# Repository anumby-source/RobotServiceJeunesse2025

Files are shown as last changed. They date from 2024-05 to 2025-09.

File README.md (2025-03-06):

# RobotServiceJeunesse2025
Développements pour la séance Service Jeunesse au printemps 2025

# Structure pour le R&D
* Chaque développeur se voit attribué un espace à son nom pour ses propres développements de R&D
* Données pour le véhicule du service jeunesse 2025

Ultérieurement, lorsque l'on aura sélectionné les choix de design et de technologie, on assemblera les développements communs

# Utilisation de Fusion 360 pour l'impression 3D

On peut démarrer cette série de tuto Youtube en mode "très débutant". Un peu lent mais clair. 1, 2, 3, 4, ...

* [Fusion 360 Complet Débutant](https://www.youtube.com/watch?v=3kL6a9yyus8&list=PL0qHSH9_1qY5kvUzO7SlggBShYAllfP7j&index=4)
* [Modélisation une Loupe en français](https://www.youtube.com/watch?v=21fNvLuIeyk&list=PL0qHSH9_1qY5kvUzO7SlggBShYAllfP7j&index=1)
* [Modélisation d'une attache type GoPro](https://www.youtube.com/watch?v=NfXD1W5tZaM&list=PL0qHSH9_1qY5kvUzO7SlggBShYAllfP7j&index=2)
* [Croquis, Contraintes, Dimensions](https://www.youtube.com/watch?v=1mFSI_tEmsY&list=PL0qHSH9_1qY5kvUzO7SlggBShYAllfP7j&index=3)
* [Tournevis à Embout - Régle d'Or, Volumes et Composants](https://www.youtube.com/watch?v=3kL6a9yyus8&list=PL0qHSH9_1qY5kvUzO7SlggBShYAllfP7j&index=4)
* [Bielle et Piston: Jointure, Articulations, Mouvements.](https://www.youtube.com/watch?v=oicK9lwJ6bA&list=PL0qHSH9_1qY5kvUzO7SlggBShYAllfP7j&index=5)
* [Organisation d'un projet et Régle d'Or](https://www.youtube.com/watch?v=NAn41hFw8Yg&list=PL0qHSH9_1qY5kvUzO7SlggBShYAllfP7j&index=6)
* [Tolérances, Historique, Colorisation](https://www.youtube.com/watch?v=N-1HDvVJG_U&list=PL0qHSH9_1qY5kvUzO7SlggBShYAllfP7j&index=7)
* [Survol des "Ateliers"](https://www.youtube.com/watch?v=0DFtvFfrYvw&list=PL0qHSH9_1qY5kvUzO7SlggBShYAllfP7j&index=8)
* [Loft et Sweep](https://www.youtube.com/watch?v=eku9RZ19Kuo&list=PL0qHSH9_1qY5kvUzO7SlggBShYAllfP7j&index=9)
* [Construction Coque de Bateau - Etape 1](https://www.youtube.com/watch?v=NDEB2YS3qxY&list=PL0qHSH9_1qY5kvUzO7SlggBShYAllfP7j&index=10)
* [Construction Coque de Bateau Etape 2](https://www.youtube.com/watch?v=uyDRabeoyRY&list=PL0qHSH9_1qY5kvUzO7SlggBShYAllfP7j&index=11)
* [Extensions (add-ins) et Scripts](https://www.youtube.com/watch?v=a0wj_iS4hvU&list=PL0qHSH9_1qY5kvUzO7SlggBShYAllfP7j&index=12)
* [Coque Minute avec Patch](https://www.youtube.com/watch?v=YINleWgpdjY&list=PL0qHSH9_1qY5kvUzO7SlggBShYAllfP7j&index=13)
* [Apprendre en faisant n'importe quoi!](https://www.youtube.com/watch?v=OFpFc8LrxU4&list=PL0qHSH9_1qY5kvUzO7SlggBShYAllfP7j&index=14)
* [Organisation, Composants, Bodies, Ensembles](https://www.youtube.com/watch?v=pDECKXFHmOQ&list=PL0qHSH9_1qY5kvUzO7SlggBShYAllfP7j&index=15)
* [Conception paramétrique sans paramètres (Où pas?)](https://www.youtube.com/watch?v=bImEM7l9Zes&list=PL0qHSH9_1qY5kvUzO7SlggBShYAllfP7j&index=16)
* [Nouvelle Interface? Pas de panique!](https://www.youtube.com/watch?v=ow5COcHA7XY&list=PL0qHSH9_1qY5kvUzO7SlggBShYAllfP7j&index=17)
* [Réconcilier (Enfin!) les Meshes avec Fusion 360](https://www.youtube.com/watch?v=rIGUrBB8rrw&list=PL0qHSH9_1qY5kvUzO7SlggBShYAllfP7j&index=18)
* [Vous allez aimer les contraintes (dans Fusion 360)](https://www.youtube.com/watch?v=fWU2rNBqDFI&list=PL0qHSH9_1qY5kvUzO7SlggBShYAllfP7j&index=19)
* [Super Mercis !!!!](https://www.youtube.com/watch?v=ioGxxQVQzVY&list=PL0qHSH9_1qY5kvUzO7SlggBShYAllfP7j&index=20)

Autre série pour Fusion 360 (2 séries: débutants, confirmés)

* [TUTORIELS FUSION 360](https://www.youtube.com/channel/UC1f3yfI3YFzhuoScarGSKwA)

TinkerCAD

* [TinkerCAD](https://www.youtube.com/watch?v=egNBQ0hXe2o)
* [TinkerCAD2](https://www.youtube.com/watch?v=DtlmVaoMNMc)

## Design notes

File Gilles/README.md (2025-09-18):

# Developpement pour le Robot Service Jeunesse 2025

<p align="center"> 
robot-2
robot-1
<p/>

<p align="center"> 
Telecommande
<p/>
  
<p align="center"> 
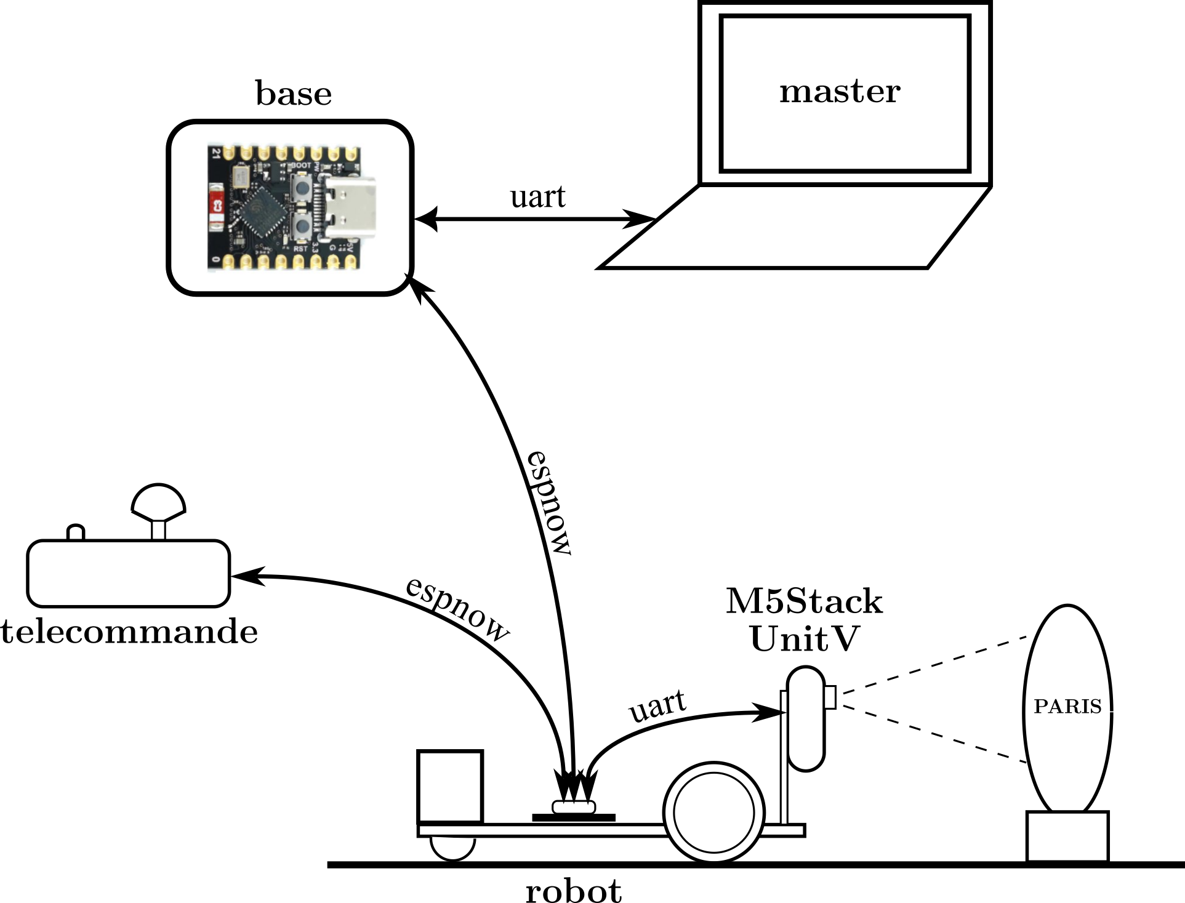
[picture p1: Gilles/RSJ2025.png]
   
<p/>

## Fonctionnement

- télécommande : elle lit la position du joystick, la transcrit en commande de vitesse des deux moteurs
  et envoie cette commande au robot à une fréquence de 10 Hz.

- M5Stack UnitV (K210) :

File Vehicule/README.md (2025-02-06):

# Dossiers pour les développements Electroniques pour le véhicule

* **Kicad** contient tous les développements électroniques
* plusieurs dossiers contiennent des documentations utilisées lors de la définition des éléments Kicad
  * **ESP32-C3**
  * **Joystick**
  * **Régulateur-DFR0569**

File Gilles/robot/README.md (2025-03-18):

## Développement robot

Les fichiers de pcb contenus dans ce répertoire sont ceux du prototype

Pour le pcb définitif, voir le répertoire **Kicad_9.0**

### Schéma électrique

<p align="center"> 
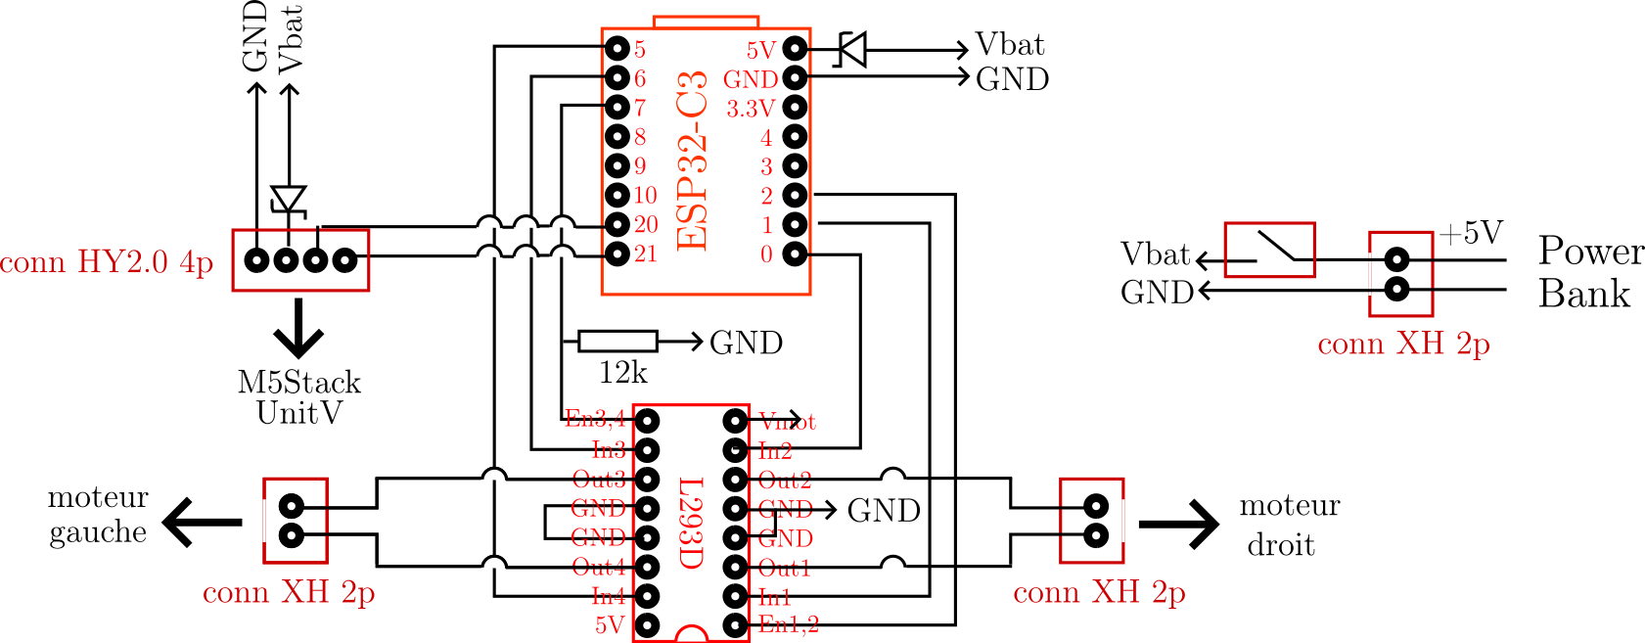
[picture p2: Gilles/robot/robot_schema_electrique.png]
   
<p/>

  ### PCB

<p align="center"> 
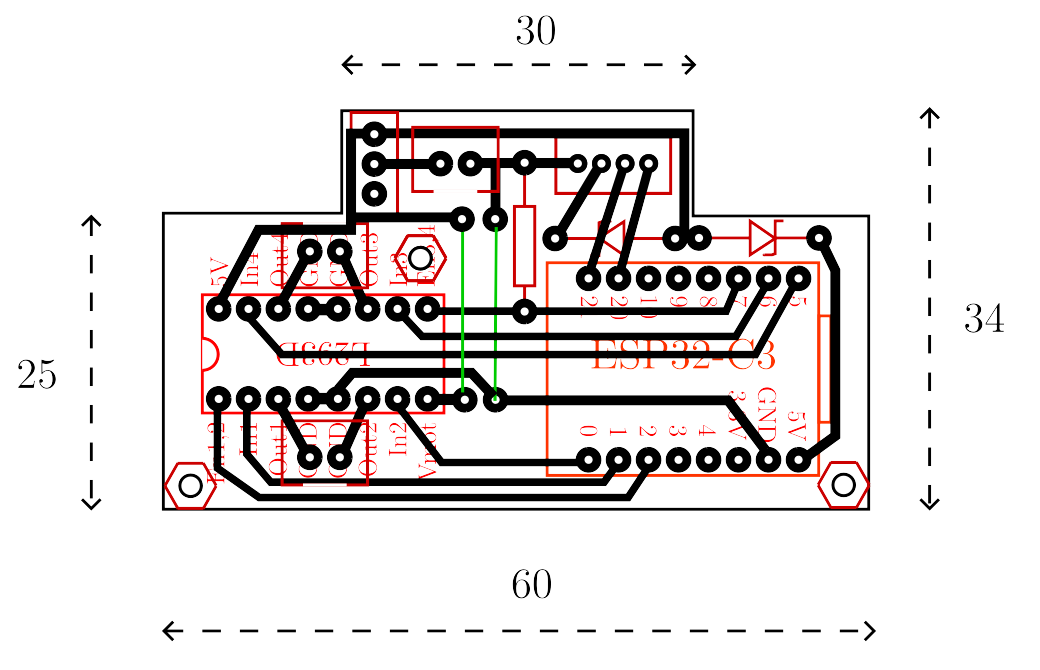
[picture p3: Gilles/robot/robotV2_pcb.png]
  
<p/>

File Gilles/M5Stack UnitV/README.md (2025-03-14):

## Reconnaissance de panneaux de signalisation avec la carte M5Stack UnitV

voir :     https://wiki.sipeed.com/soft/maixpy/en/course/ai/image/self_learn_classifier.html

### 1) Créer un compte sur MaixHub : 
    
    https://maixhub.com

### 2) Récupération du code machine du module M5Stack UnitV (nécessaire pour télécharger le modèle):
   
   voir https://maixhub.com/share/6
   - se logger sur le site MaixHub
   - télécharger key.gen.bin (https://dl.sipeed.com/shareURL/MaixHub_Tools) et le flasher avec 
     kflash_gui sur la carte UnitV à l'adresse 0X000000
   - lancer un terminal (screen, putty, …) et rebooter la carte. Le code apparait dans la fenêtre.

### 3) Installer le firmware : 

Flasher le firmrware (fichier _M5StickV_Firmware_v5.1.2.kfpkg_) avec kflash_gui

Flash firmware

### 4) Télécharger le modèle sur MaixHub (utiliser le code machine récupéré au 2) ) :
     
     https://maixhub.com/model/zoo/61
   
et le charger sur la carte avec kflash_gui à l'adresse 0X300000

Flash kmodel

### 5) Sur une carte micro-SD, charger _3_panneaux.classifier_ et _classify.py_
   
Inserer la carte micro-SD dans le M5Stack UnitV et lancer le script _classify.py_ 

Il est aussi possible de charger des fichiers (en particulier 3_panneaux.classifier) directement dans la mémoire flash de la M5Stack UnitV, sans utiliser la carte SD, dans MaixPy IDE : onglet "Tools > transfert file to board".

Pour chaque panneau reconnu, la led de la carte s'allume :
   - rouge -> stop
   - vert -> sens interdit
   - bleu -> dépassement interdit

## Connecteur Grove 

* 4 - GND noir
* 3 - VCC orange
* 2 - TX/SDA jaune
* 1 - RX/SCL blanc

* 
* 
*

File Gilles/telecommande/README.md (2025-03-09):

## Développements télécommande

Les fichiers de pcb contenus dans ce répertoire sont ceux du prototype

Pour le pcb définitif, voir le répertoire **Kicad_9.0**

### PCB - Implantation
<p align="center"> 
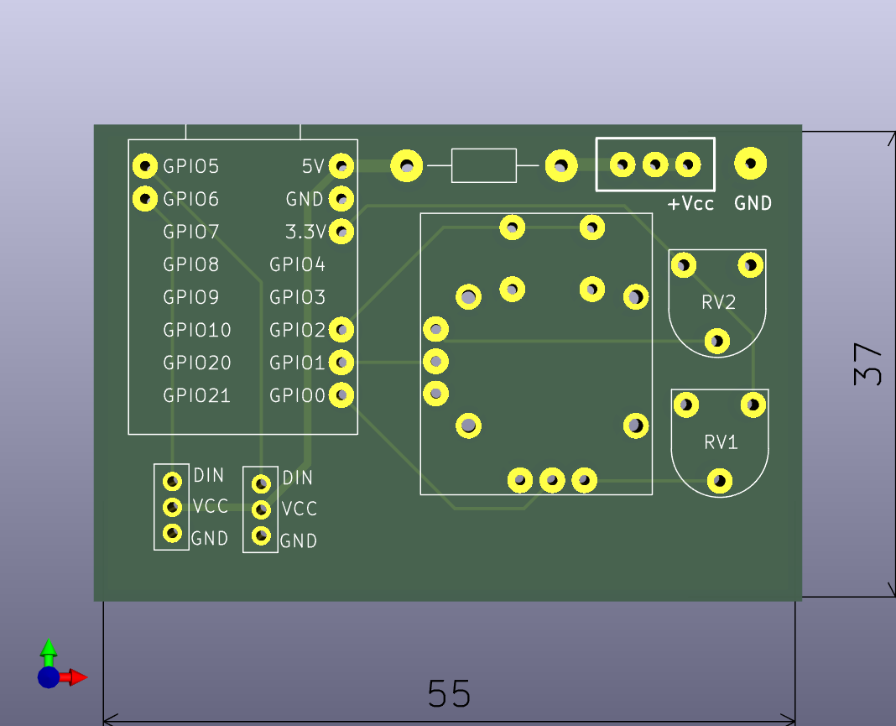
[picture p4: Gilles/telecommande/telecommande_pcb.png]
  
<p/>

### PCB - Typon
<p align="center"> 
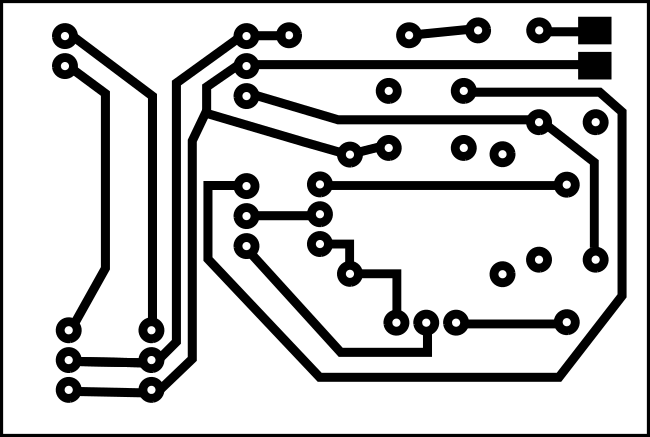
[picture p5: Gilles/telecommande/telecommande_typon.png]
  
<p/>

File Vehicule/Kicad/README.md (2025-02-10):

# On a installé Kicad v8

Puis on ajoute la librairie expressif qui fournit entre autres, les composants Kicad associés au ESP32-C3

https://github.com/espressif/kicad-libraries/tree/legacy_kicad7

La librairie est donc le fichier zip  espressif-kicad-addon.zip

Il faut utiliser l'outil "Gestionnaire de pluin et de contenu" qui va directement installer la librairie expressif à partir du fichier zib précédemment téléchargé

J'ai ajouté dans la librairie "Expressif" les composants nécessaires pour "esp32-c3-supermini" qui n'existaient pas dans la librairie de base

https://github.com/SurrealityLabs/esp32c3-wled

Mise à jour de la librairie (installée dans le commit)

"expressif-kicad-addon.zip"

# Nos développements pour le projet RobotJeunesse

Lors des développements effectués dans le cadre du Robot, j'ai été amenée à créer plusieurs éléments Kicad:
- des symboles,
- des empreintes associées

Ces éléments sont installés dans deux librairies:

1) https://github.com/anumby-source/RobotServiceJeunesse2025/blob/main/Vehicule/Kicad/Anumby.kicad_sym
2) https://github.com/anumby-source/RobotServiceJeunesse2025/tree/main/Vehicule/Kicad/Empreintes.pretty

Si vous souhaitez utiliser Kicad, pour développer dans le cadre de nos projets actuels, vous devrez importer ces librairies dans votre version de Kicad, ainsi les deux projets en cours seront modifiables:

1) https://github.com/anumby-source/RobotServiceJeunesse2025/tree/main/Vehicule/Kicad/T%C3%A9l%C3%A9commande
2) https://github.com/anumby-source/RobotServiceJeunesse2025/tree/main/Vehicule/Kicad/Robot

[Outil 3D](https://circuitcellar.com/research-design-hub/basics-of-design/create-3d-models-of-components-and-board-outlines-in-kicad/)

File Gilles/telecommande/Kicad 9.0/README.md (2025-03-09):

###  Fichiers Kicad pour le PCB de la télécommande

Contient entre autres des symboles et empreintes spécifiques au PCB de la télécommande (suppression des broches non utilisées 

de l'ESP32-C3_mini, diode neopixel à 3 broches)

<p align="center"> 
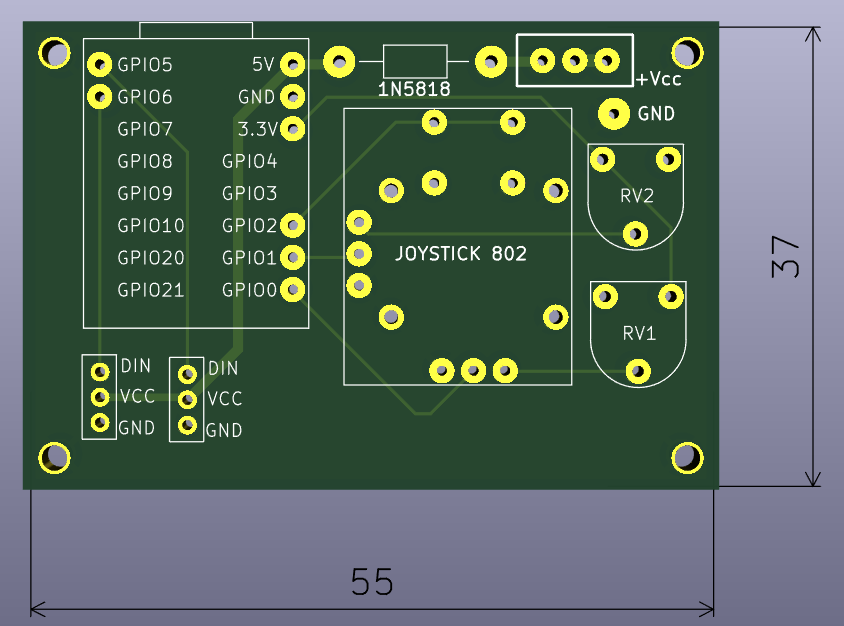
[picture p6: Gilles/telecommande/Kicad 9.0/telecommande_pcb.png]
  
<p/>

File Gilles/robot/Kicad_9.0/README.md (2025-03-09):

###  Fichiers Kicad pour le PCB du robot

Contient entre autres des symboles et empreintes spécifiques au PCB du robot (suppression des broches non utilisées 

de l'ESP32-C3_mini)

<p align="center"> 
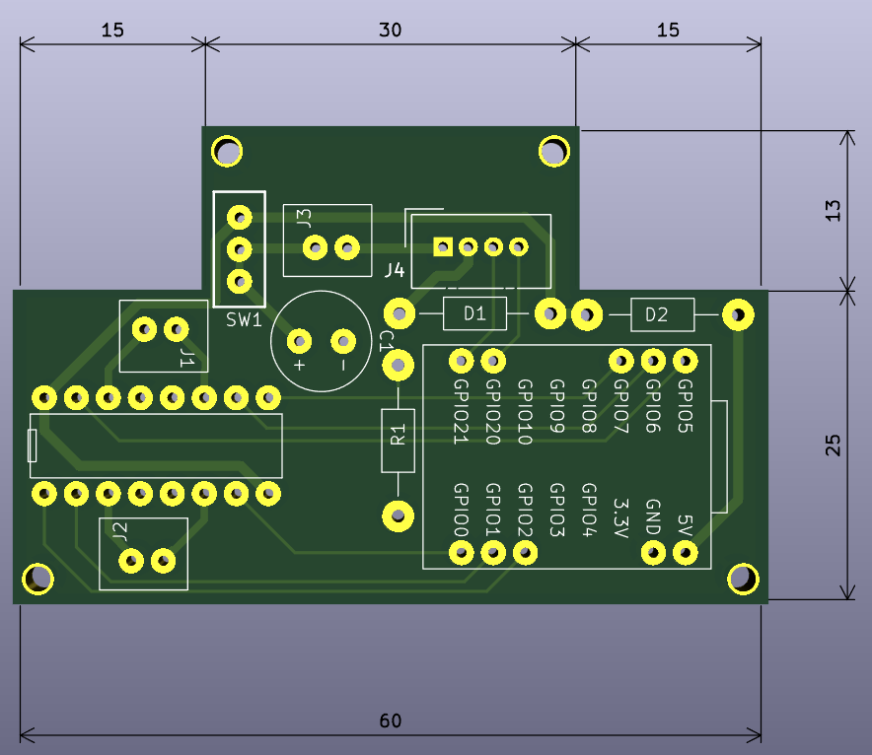
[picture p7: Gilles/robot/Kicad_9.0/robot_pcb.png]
  
<p/>

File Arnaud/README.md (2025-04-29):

vous trouverez dans le wiki un essai sous Linux réalisé avant la compétition pour avoir une deuxième installation indépendante

Arnaud

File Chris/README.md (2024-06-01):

# Petit essai avec l'environment Flask

L'application Chris/flask/app.py est lancée par la commande

- ```> cd Chris/flask```
- ```> flask run```

# Essais avec Javascript

- [Manuel Javascript](https://fr.javascript.info/)
- [Norme JS](https://spec.whatwg.org/)
- [Doc Mozilla](https://developer.mozilla.org/en-US/search)
- Ask JS: MDN [terme]

## Première version d'une interface pour piloter un robot

On peut faire bouger le robot en avant, à gauche, à droite, en arrière

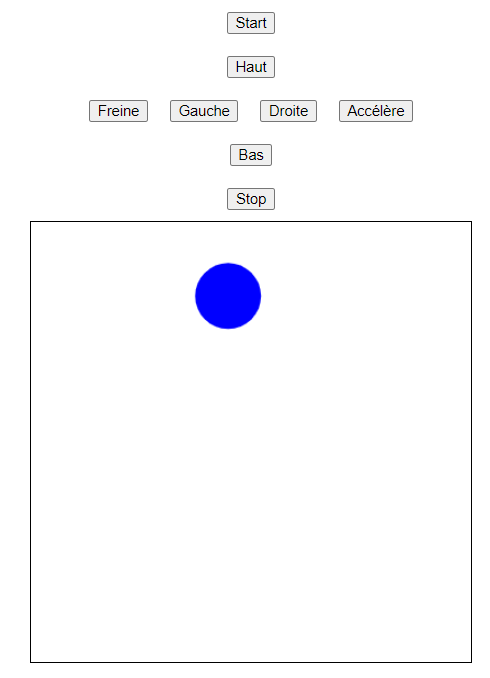
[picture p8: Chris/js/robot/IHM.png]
IHM


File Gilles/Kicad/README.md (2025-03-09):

### Symboles et empreintes de composants, non spécifiques au projet RSJ2025

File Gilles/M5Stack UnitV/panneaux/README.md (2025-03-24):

## Fichiers panneaux signalisation et villes

<p align="center"> 
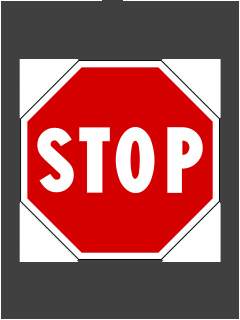
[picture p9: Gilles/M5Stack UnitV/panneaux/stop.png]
   
<p/>

<p align="center"> 
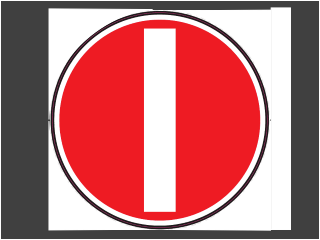
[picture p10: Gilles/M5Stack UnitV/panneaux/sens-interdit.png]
   
<p/>

<p align="center"> 
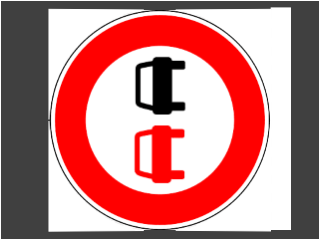
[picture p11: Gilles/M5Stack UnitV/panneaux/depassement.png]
   
<p/>

<p align="center"> 
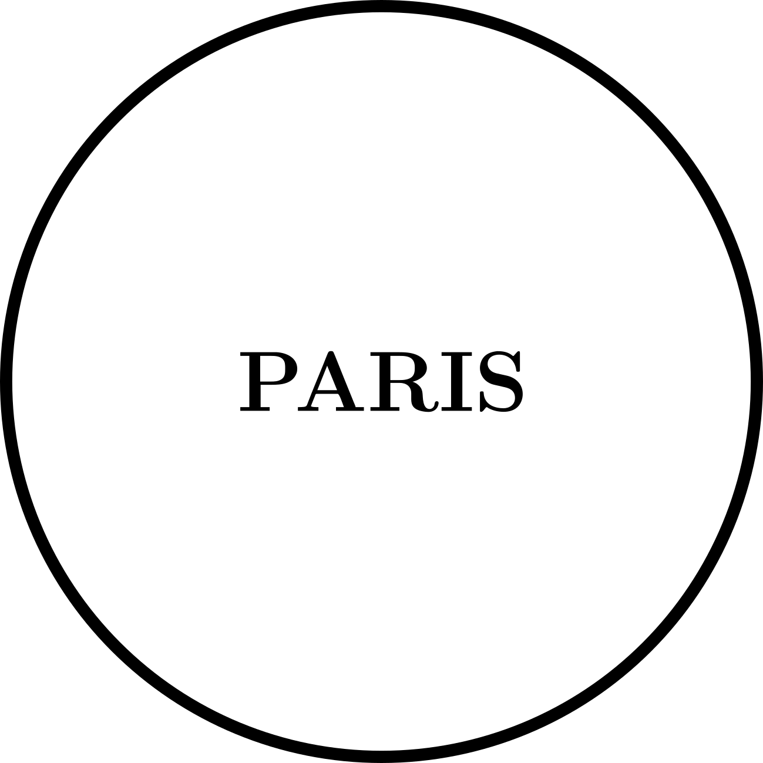
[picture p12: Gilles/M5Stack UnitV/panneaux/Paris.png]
   
<p/>

<p align="center"> 
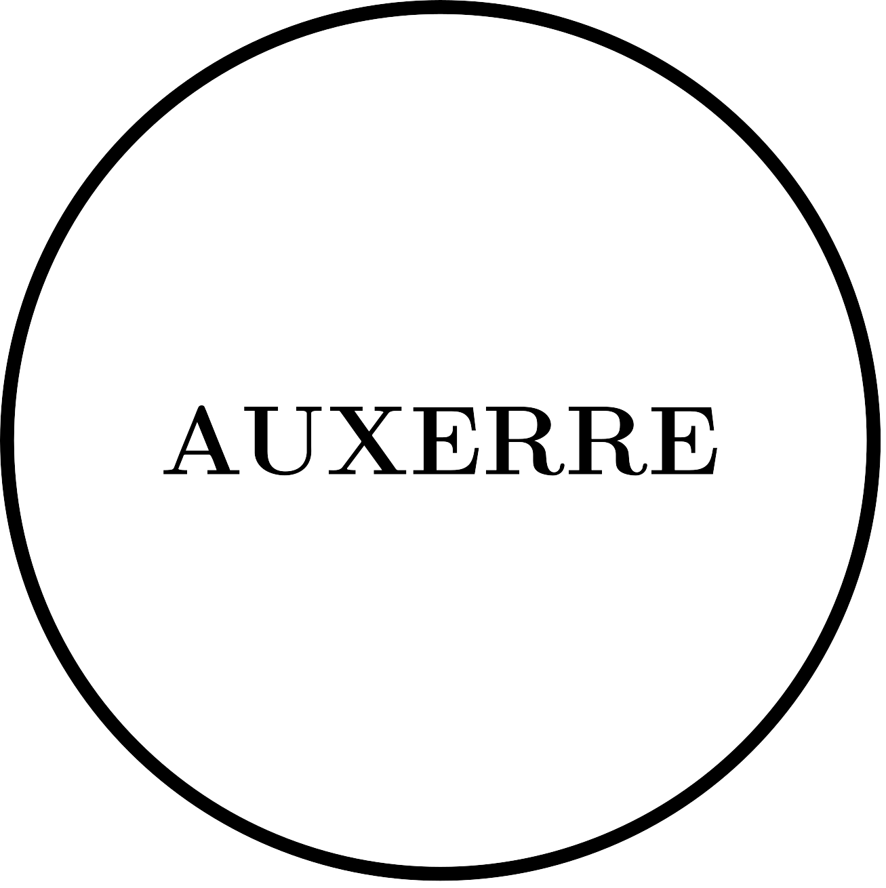
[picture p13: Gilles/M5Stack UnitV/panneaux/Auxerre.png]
   
<p/>

<p align="center"> 
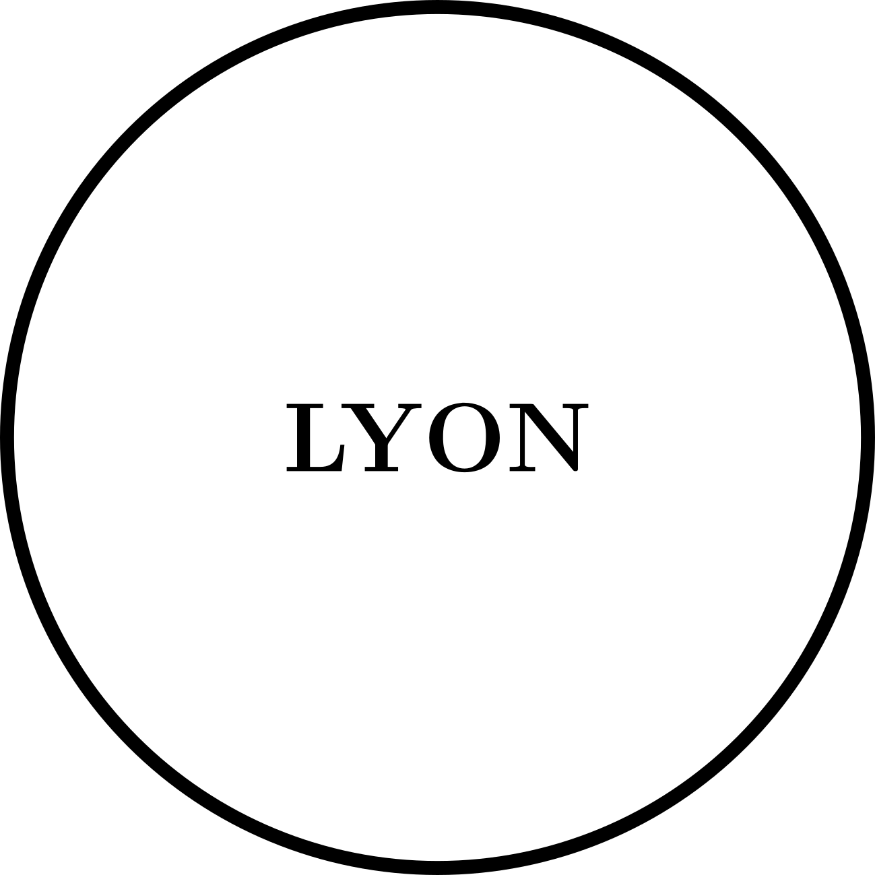
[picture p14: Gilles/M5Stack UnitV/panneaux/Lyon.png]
   
<p/>

<p align="center"> 
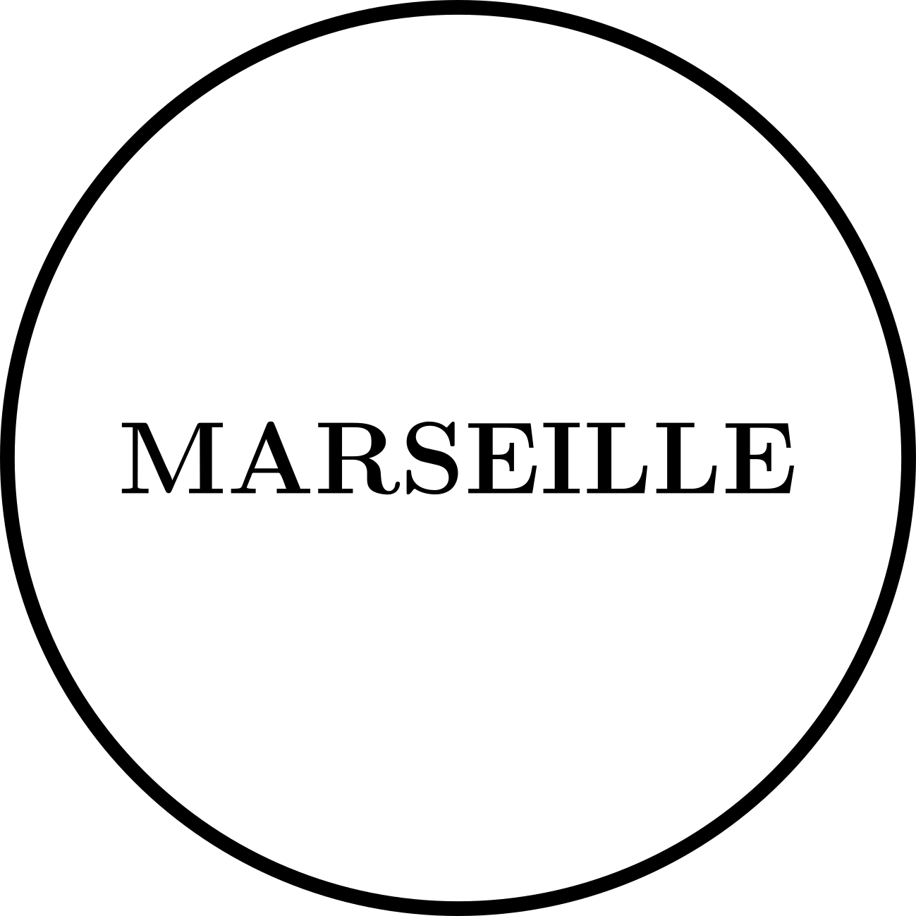
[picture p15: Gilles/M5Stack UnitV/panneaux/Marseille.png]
   
<p/>

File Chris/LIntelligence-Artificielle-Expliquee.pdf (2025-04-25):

# L'Intelligence Artificielle Anumby 25 avril 2025

L'IA est la capacité des machines à imiter l'intelligence humaine. Elle peut aider à résoudre des problèmes complexes et peut aider à prendre des décisions.

Mais… cela soulève beaucoup de questions très importantes sur son utilisation qui peut être parfois très problématique :

- On peut maintenant facilement produire des textes, des photos, des films qui semblent refléter la réalité, la “vérité”, ou qui semblent avoir été produites par un humain mais qui ne le sont pas du tout !!!
- Où est la vérité ? Attention aux malveillants…
- Pour fonctionner, l’IA a besoin de quantités d’énergie gigantesques, infiniment

plus grande que ce que le cerveau humain demande.
- Sans parler de l’eau nécessaire pour refroidir les centres de calcul.

# Les Débuts de l'IA

## Années 1950

Naissance de l'IA comme discipline scientifique.

## Test de Turing

Alan Turing propose une méthode pour évaluer l'intelligence des machines.

## Premiers programmes d’échecs 1952

Développement de jeux d'échecs et systèmes logiques simples.

## Invention du terme Intelligence Artificielle 1956

## Système expert 1980

# L'Évolution de l'IA

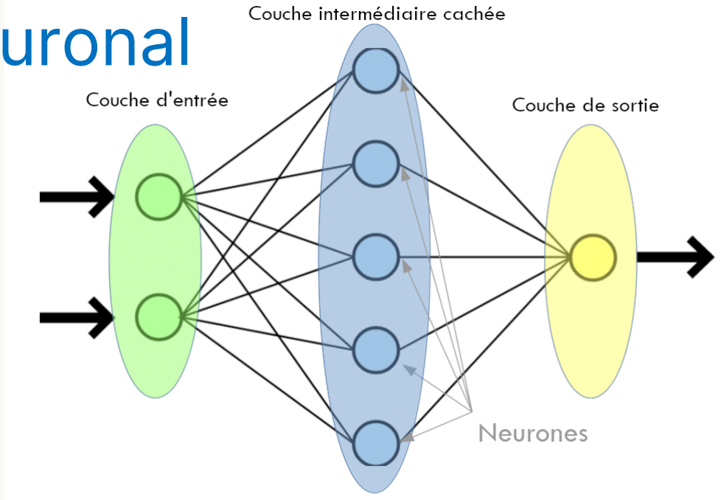
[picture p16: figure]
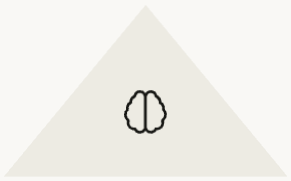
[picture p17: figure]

## Deep Learning (= Apprentissage profond)

Réseaux neuronaux complexes imitant le cerveau

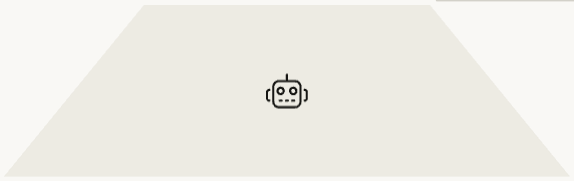
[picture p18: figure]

## Machine Learning (= Apprentissage par les machines)

Algorithmes apprenant des données

## Systèmes Experts

Programmes basés sur des règles fixes

# Réseau neuronal

# L'IA au Quotidien :

## "Le chat" outil français (introduit par la société Mistral)

“ChatGPT” produit par la
société américaine OpenAI
(liée à MicroSoft)

## De très nombreux outils spécialisés ont été produits dans le monde entier désormais, dans tous les domaines:

- technologiques,
- culturels,
- scientifiques,
- médicaux,
- juridiques,

## - financier

Les outils conversationnels (ChatBOT) permettent à un humain de soumettre une question, ou une réflexion à une IA distante, qui fouillera dans sa base d’apprentissage, et fournira en retour un texte, une image, en correspondance “plausible” (statistiquement) avec la question posée.

# Comment l'IA Apprend : Le "Machine Learning"

## Apprentissage Supervisé

Apprend d'exemples étiquetés

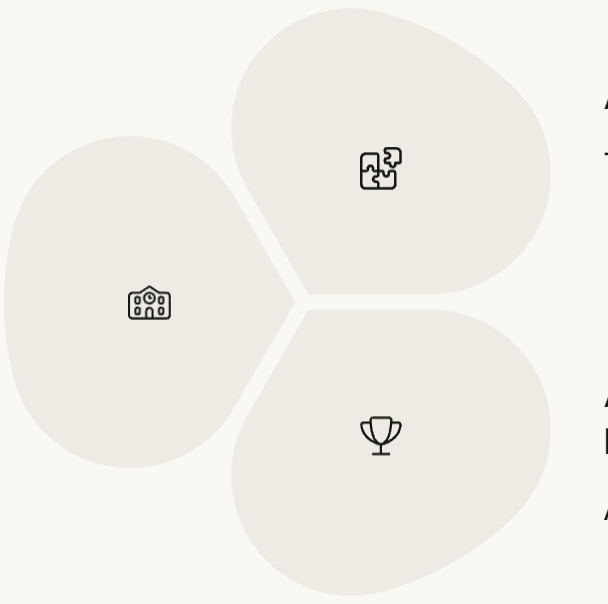
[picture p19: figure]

## Apprentissage Non Supervisé

Trouve des motifs sans guide

## Apprentissage par Renforcement

Apprend par essais et erreurs

# Comment l'IA Décide : Les Algorithmes

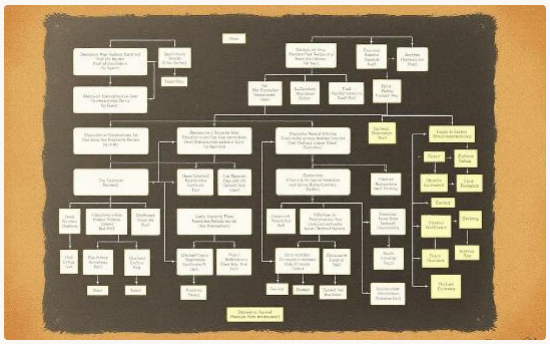
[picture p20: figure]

## Arbres de Décision

Séquences logiques de choix basés sur des critères spécifiques.

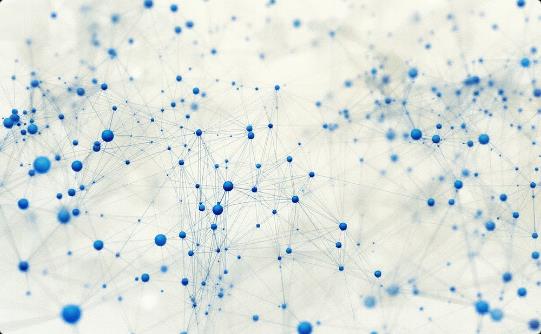
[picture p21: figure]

## Réseaux de Neurones

Modèles inspirés du cerveau humain, apprenant par connexions.

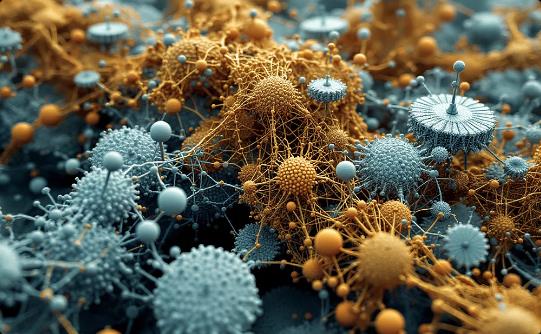
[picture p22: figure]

## Autres Algorithmes

Diverses méthodes mathématiques pour différents types de problèmes.

# L'IA : Un Avenir Prometteur… si tout se passe bien … énergie ? … société ? … emploi ?

## Santé

Amélioration du diagnostic médical

## Transport

Véhicules autonomes en
développement

## Finance

Détection de fraude optimisée

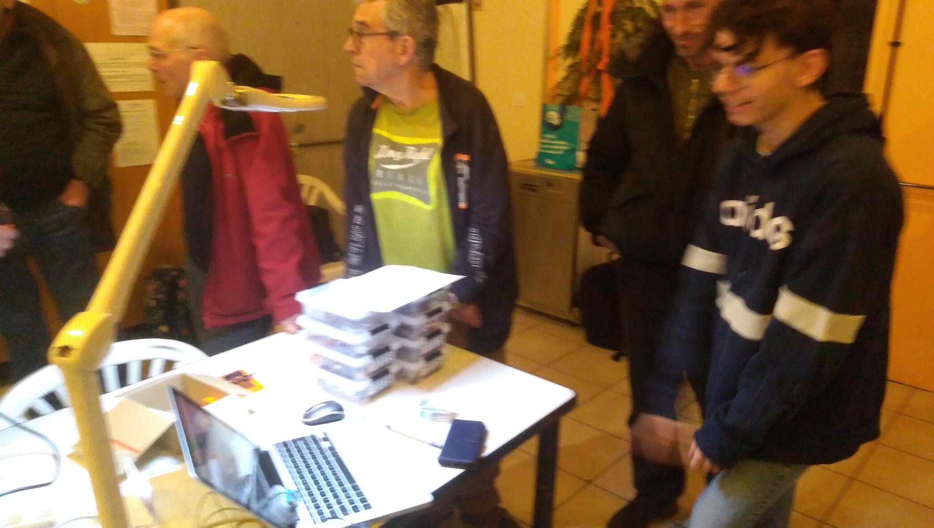
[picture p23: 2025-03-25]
Arnaud/préparation.jpeg

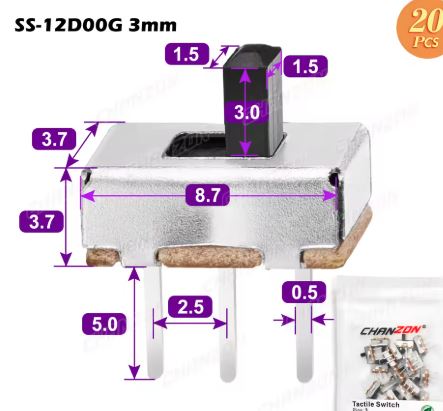
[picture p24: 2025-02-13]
Vehicule/Switch/switch.jpg

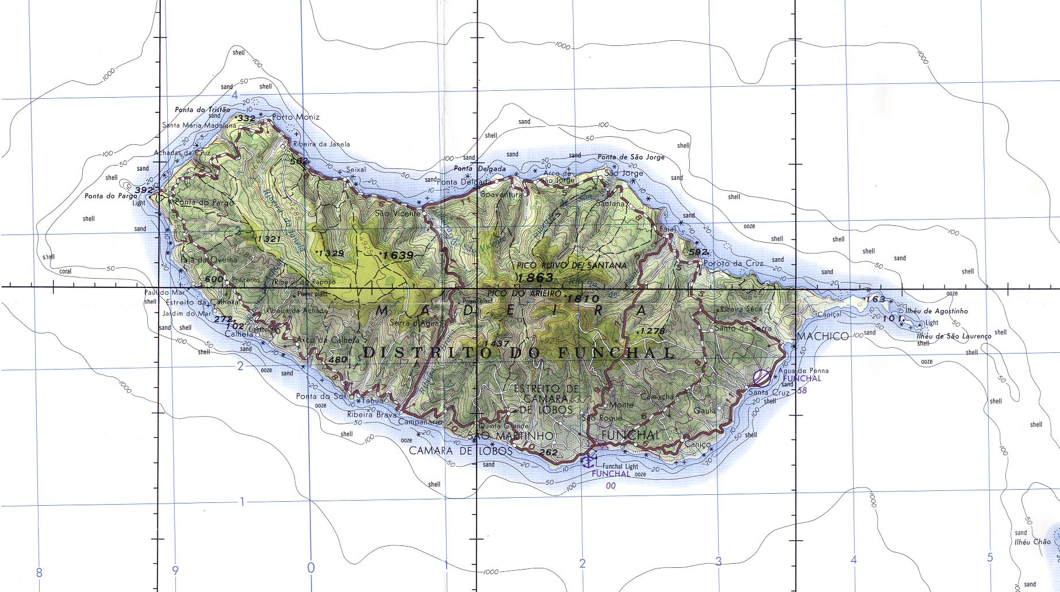
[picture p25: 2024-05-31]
Chris/js/demo/Madeira-71.jpg

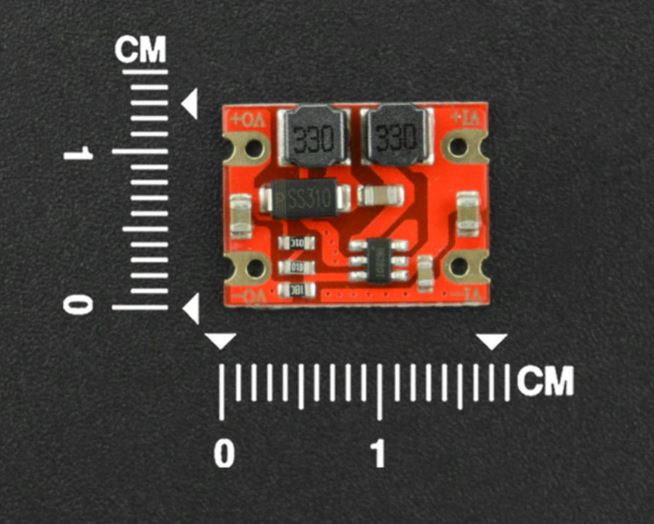
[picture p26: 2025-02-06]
Vehicule/Régulateur DFR0569/dimensions.jpg

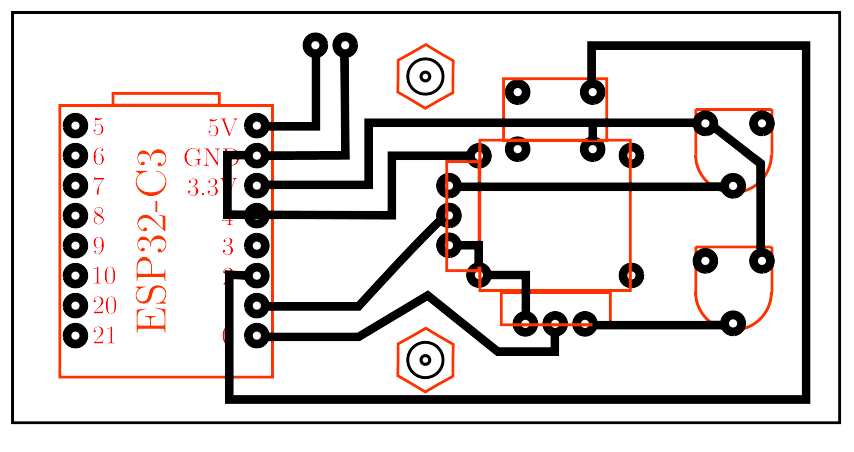
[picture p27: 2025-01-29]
Vehicule/schema electrique telecommande.png

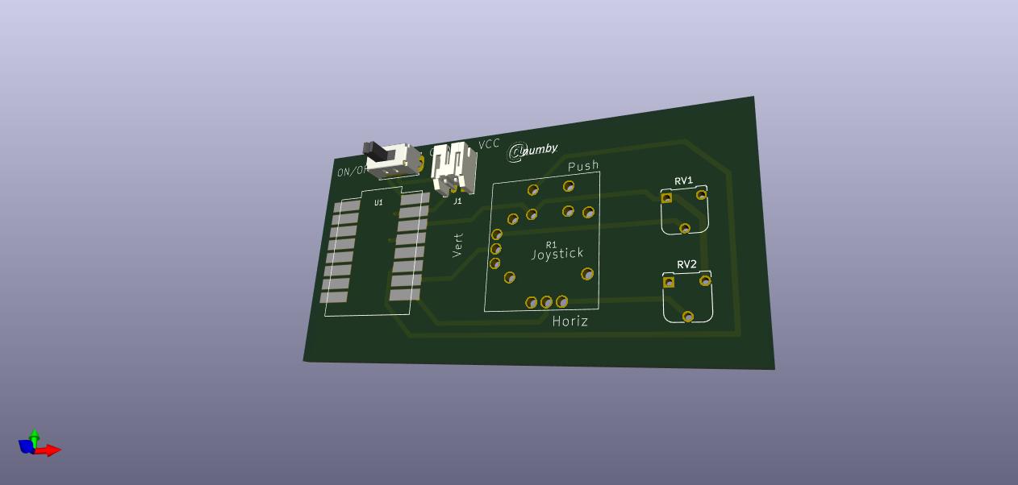
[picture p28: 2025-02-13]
Vehicule/Kicad/Télécommande/Télecommande.jpg

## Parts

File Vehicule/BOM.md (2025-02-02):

Robot:

* 2 [roues](https://fr.aliexpress.com/item/1005005856944082.html)
* 1 [coupleur de piles LR6 (AA)](https://fr.aliexpress.com/item/1005005473817204.html)
* 1 [driver de moteur CC](https://fr.aliexpress.com/item/1005007167556348.html)
* 1 [roue arrière](https://fr.aliexpress.com/item/1005005888599065.html)
* 1 [interrupteur](https://fr.aliexpress.com/item/1005003938856402.html)
* [barrette de headers femelle](https://fr.aliexpress.com/item/1802112582.html)
* [barrette de headers male](https://fr.aliexpress.com/item/32758380907.html)
* 1 [régulateur de tension](https://www.gotronic.fr/art-regulateur-5-vcc-dfr0569-29560.htm)
* 1 [diode Schottky](https://fr.aliexpress.com/item/1005006139982770.html)
* 1 [connecteur PH2.0](https://fr.aliexpress.com/item/1005007389108799.html)
* 8 [vis M2 8mm](https://fr.aliexpress.com/item/32810852732.html)
* 8 [écrous M2](https://fr.aliexpress.com/item/1005007593861199.html)
* 2 [vis M2.5 8mm](https://fr.aliexpress.com/item/32810852732.html)
* 2 [écrous M2.5](https://fr.aliexpress.com/item/1005007593861199.html)
* 3 piles LR6 (AAA) 

Télécommande :

* 1 [joystick](https://fr.aliexpress.com/item/1005005845121833.html)
* 1 [esp32-C3 mini](https://fr.aliexpress.com/item/1005007496189056.html)
* 2 [trimmers](https://fr.aliexpress.com/item/1005005282375532.html)
* 1 [coupleur de piles LR03 (AAA)](https://fr.aliexpress.com/item/1005001407817768.html)
* 1 [connecteur PH2.0](https://fr.aliexpress.com/item/1005007389108799.html)
* 2 [vis M2.5 8mm](https://fr.aliexpress.com/item/32810852732.html)
* 2 [écrous M2.5](https://fr.aliexpress.com/item/1005007593861199.html)

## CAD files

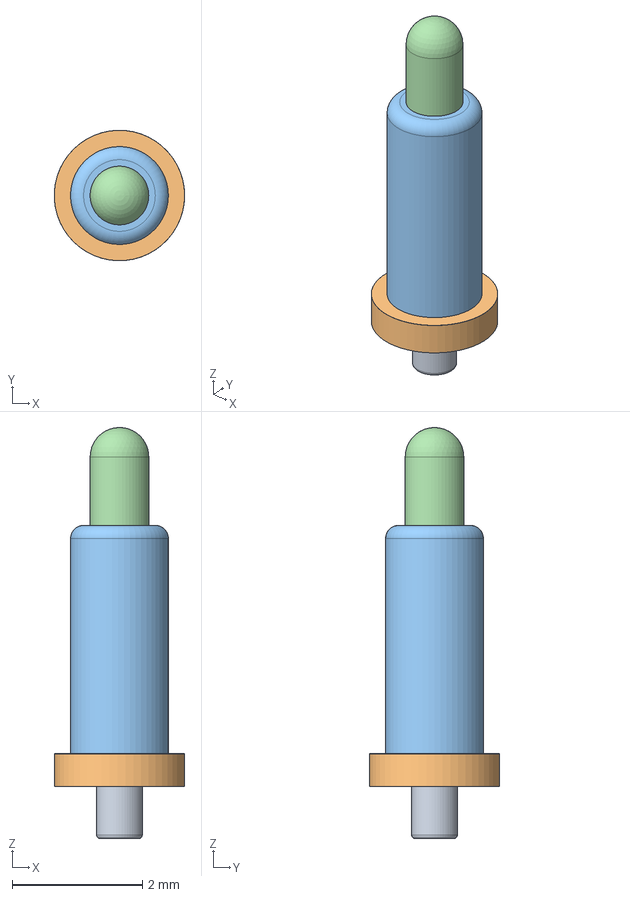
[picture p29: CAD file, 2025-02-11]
CadQuery/pogo_pin.step
2.00 x 2.00 x 6.30 mm
828ed527-e7b2-11ef-93d7-7c76357cb7d6_part
8290a9ea-e7b2-11ef-8b9f-7c76357cb7d6_part
82936908-e7b2-11ef-a14e-7c76357cb7d6_part
82953f1e-e7b2-11ef-893e-7c76357cb7d6_part

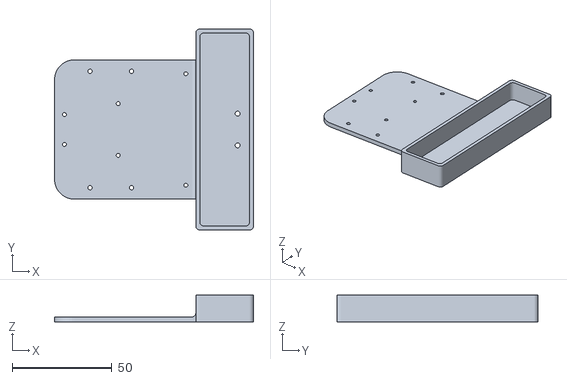
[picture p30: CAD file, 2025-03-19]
Gilles/fichiers stl/robot/chassis.stl
100.0 x 101.0 x 13.5

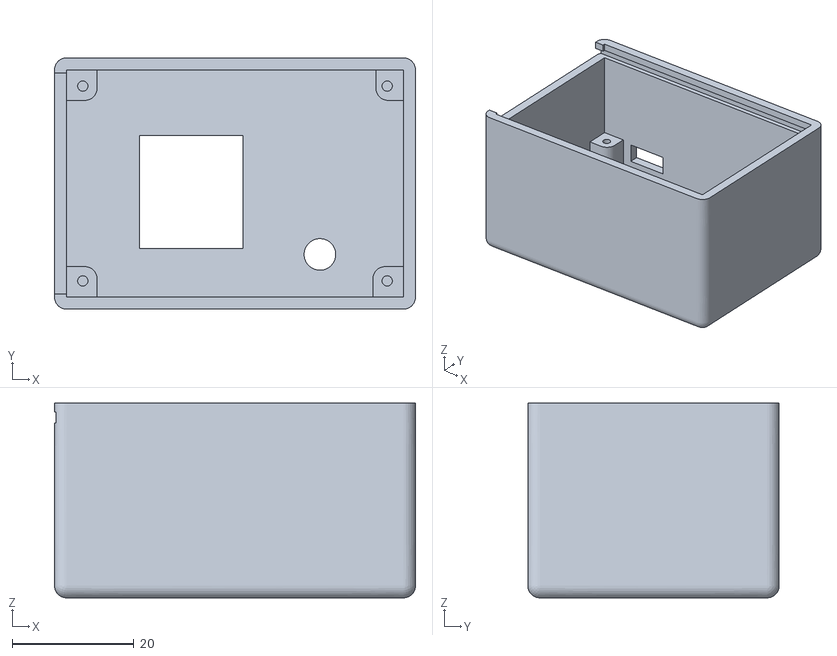
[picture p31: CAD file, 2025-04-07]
Gilles/fichiers stl/telecommande/telecommande.stl
59.3 x 41.3 x 32.0

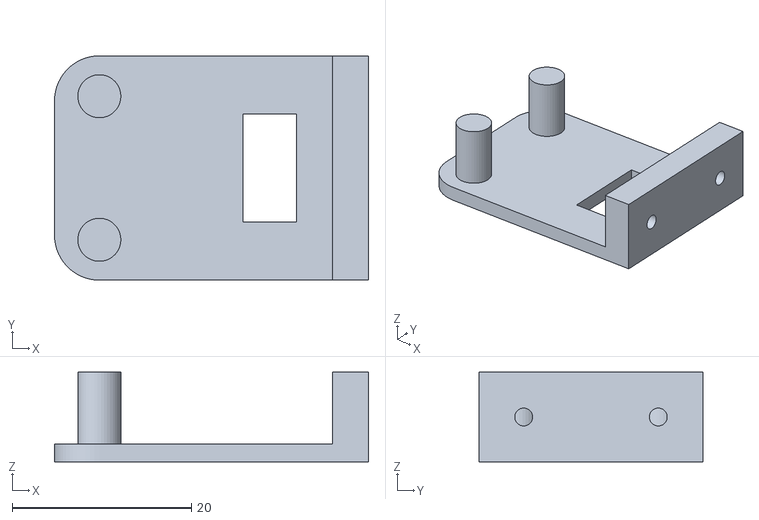
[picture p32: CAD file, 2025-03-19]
Gilles/fichiers stl/robot/support UnitV.stl
35.0 x 25.0 x 10.0

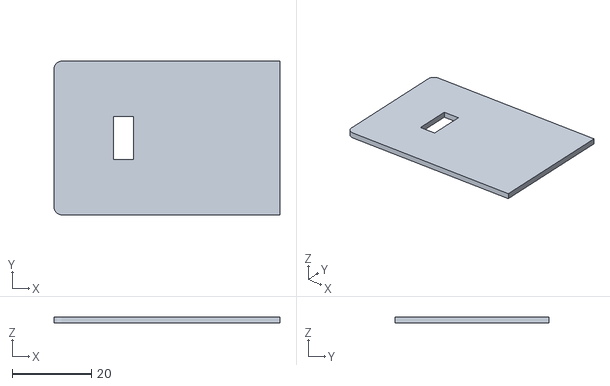
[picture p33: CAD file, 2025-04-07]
Gilles/fichiers stl/telecommande/couvercle.stl
57.0 x 38.8 x 1.60

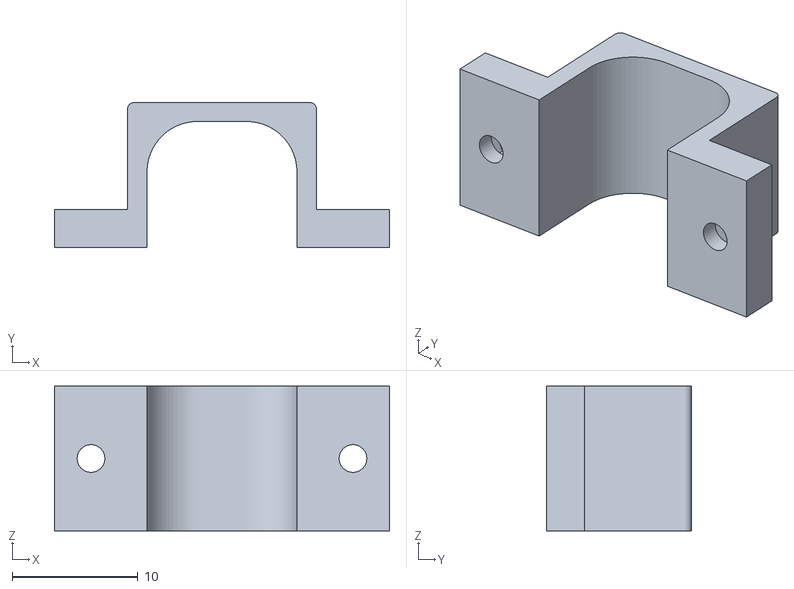
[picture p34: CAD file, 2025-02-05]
Gilles/fichiers stl/robot/fixation moteur.stl
26.6 x 11.5 x 11.5

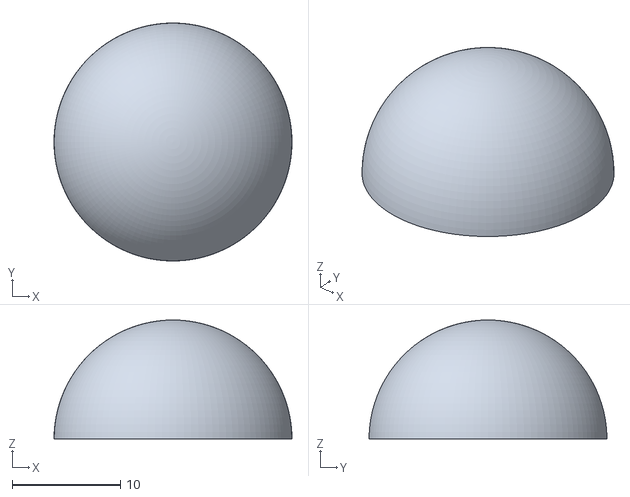
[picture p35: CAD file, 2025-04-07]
Gilles/fichiers stl/telecommande/joystick bouton.stl
22.0 x 22.0 x 11.0

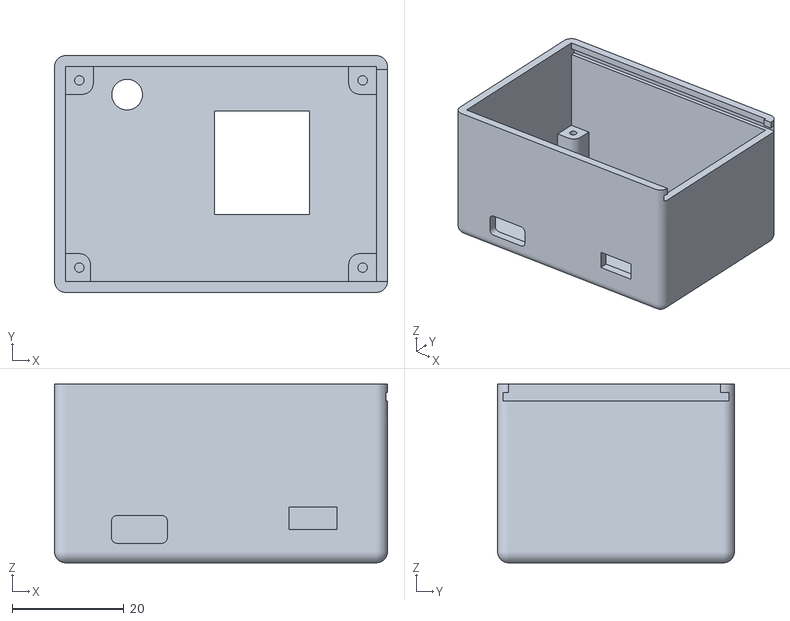
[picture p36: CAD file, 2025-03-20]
Gilles/fichiers stl/telecommande/boitier telecommande.stl
59.6 x 42.4 x 32.0

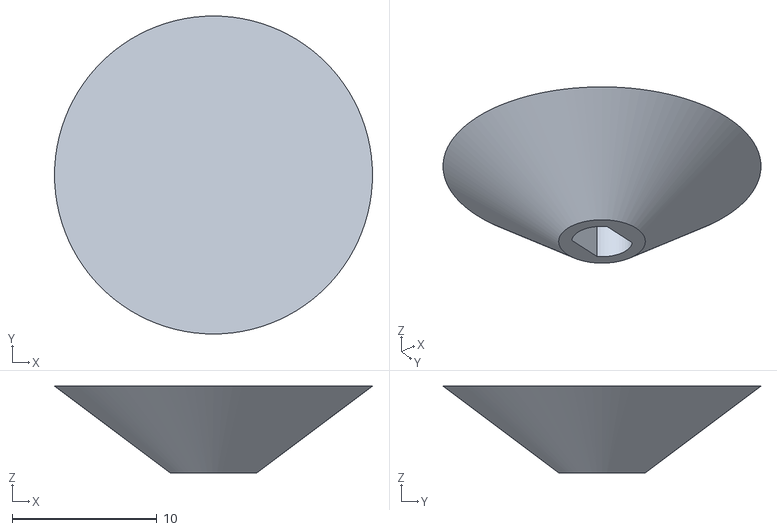
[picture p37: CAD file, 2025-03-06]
Gilles/fichiers stl/telecommande/joystick base.stl
22.0 x 22.0 x 6.00

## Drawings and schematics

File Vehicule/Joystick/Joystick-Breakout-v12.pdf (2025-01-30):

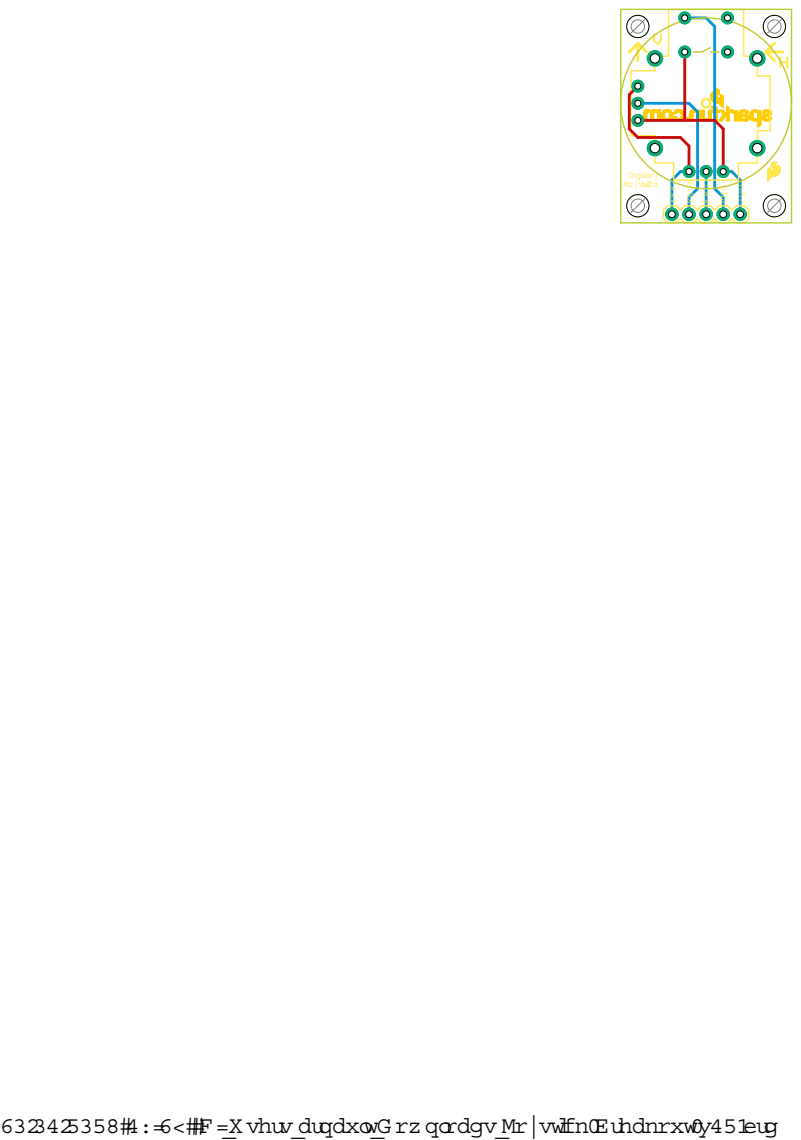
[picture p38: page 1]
30/01/2025 17:39 C:\U sers\arnault\D ow nloads\Joystick-Breakout-v12.brd VCC; VERT; HORZ; SEL; GND; Analog Joystick

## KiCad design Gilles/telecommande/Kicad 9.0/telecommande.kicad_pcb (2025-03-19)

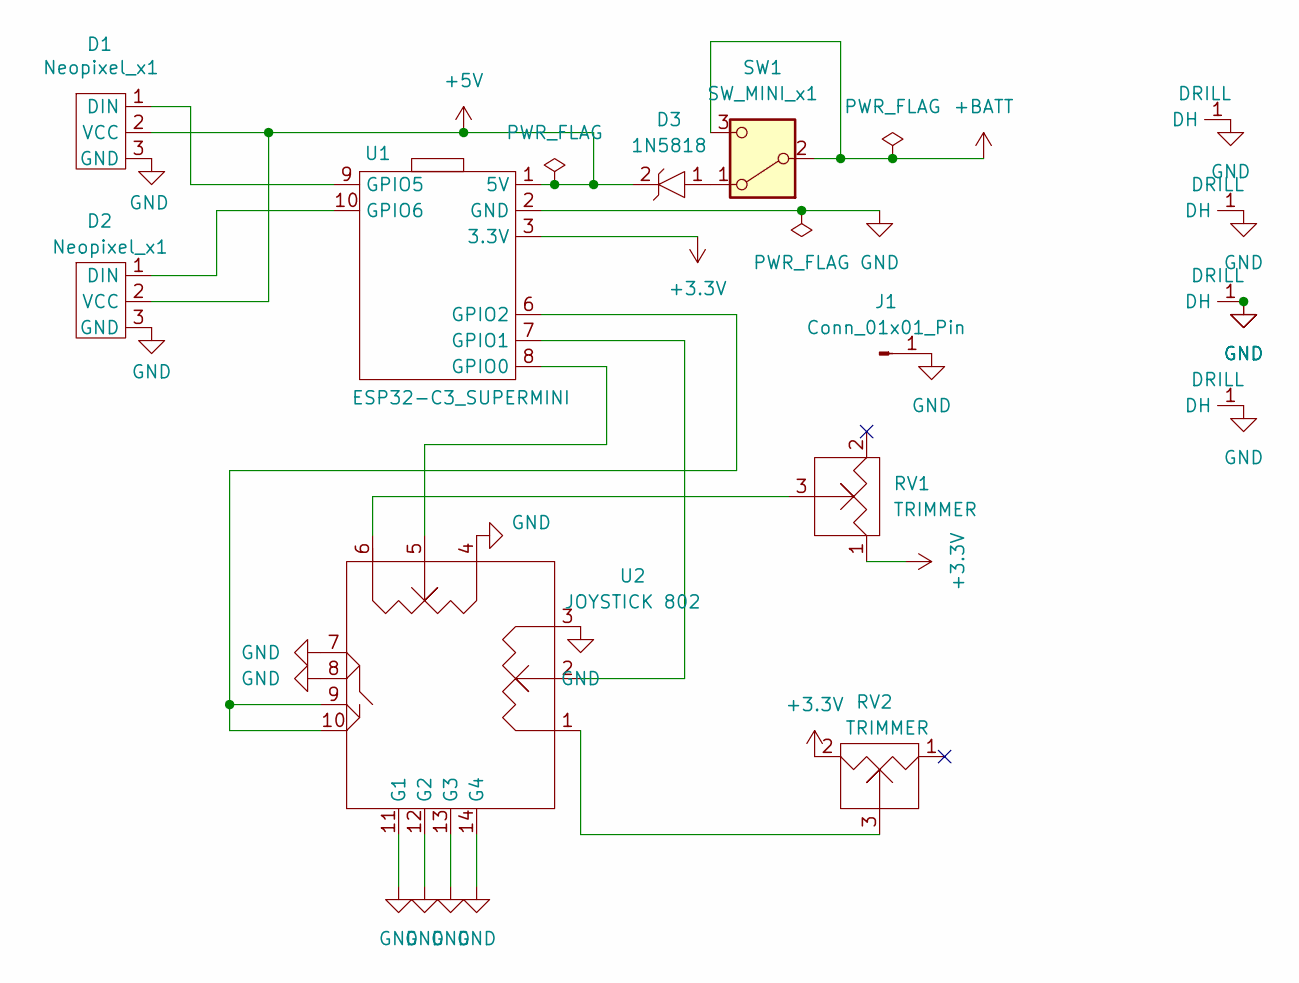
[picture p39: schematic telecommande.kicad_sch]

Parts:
D1, D2: Neopixel_x1
D3: 1N5818
DH1, DH2, DH3, DH4: DRILL; DRILL_HOLE
J1: Conn_01x01_Pin; SINGLE PIN
RV1, RV2: TRIMMER
SW1: SW_MINI_x1; SW_MINI_X1
U1: ESP32-C3_SUPERMINI
U2: JOYSTICK 802; JOYSTICK_MODEL_802

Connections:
+3.3V: RV1.1, RV2.2, U1.3 (3.3V)
+5V: D1.2 (VCC), D2.2 (VCC), D3.2, U1.1 (5V)
+BATT: SW1.2 (B), SW1.3 (C)
GND: D1.3 (GND), D2.3 (GND), DH1.1 (DH), DH2.1 (DH), DH3.1 (DH), DH4.1 (DH), J1.1, U1.2 (GND), U2.3, U2.4, U2.7, U2.8, U2.11 (G1), U2.12 (G2), U2.13 (G3), U2.14 (G4)
unnamed: D1.1 (DIN), U1.9 (GPIO5)
unnamed: D2.1 (DIN), U1.10 (GPIO6)
unnamed: RV1.3, U2.6
unnamed: RV2.3, U2.1
unnamed: D3.1, SW1.1 (A)
unnamed: U1.8 (GPIO0), U2.5
unnamed: U1.7 (GPIO1), U2.2
unnamed: U1.6 (GPIO2), U2.9, U2.10

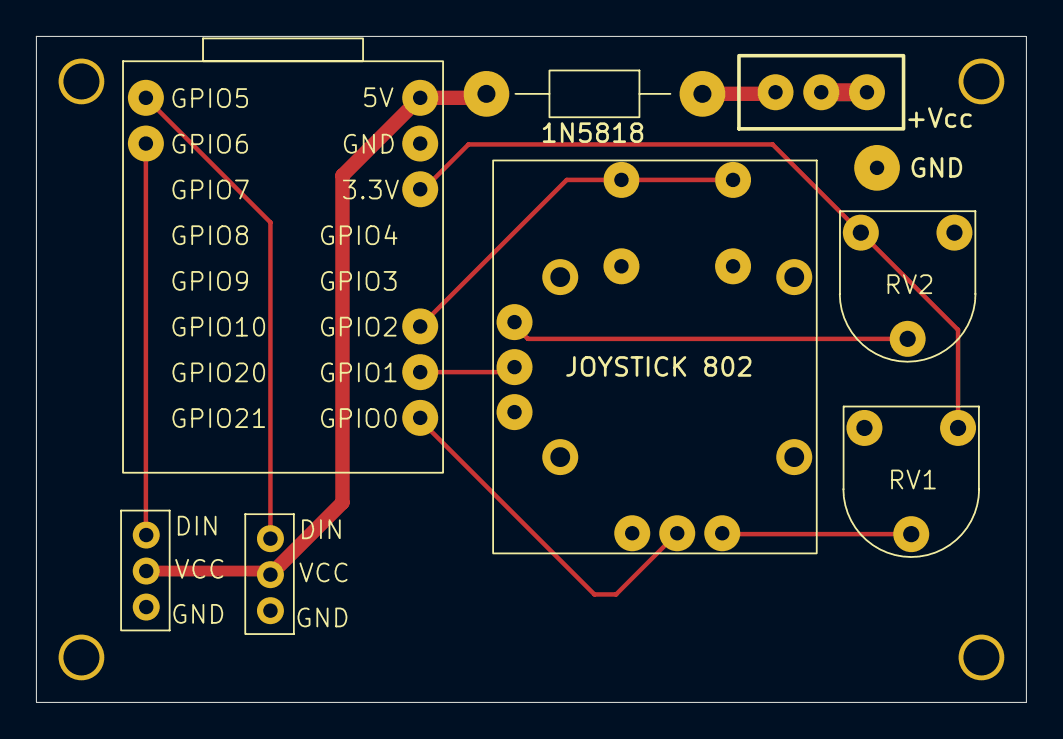
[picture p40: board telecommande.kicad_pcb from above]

Board: 2 copper layers, 55.0 x 37.0 mm, 13 parts (0 on the bottom side), 12 nets.

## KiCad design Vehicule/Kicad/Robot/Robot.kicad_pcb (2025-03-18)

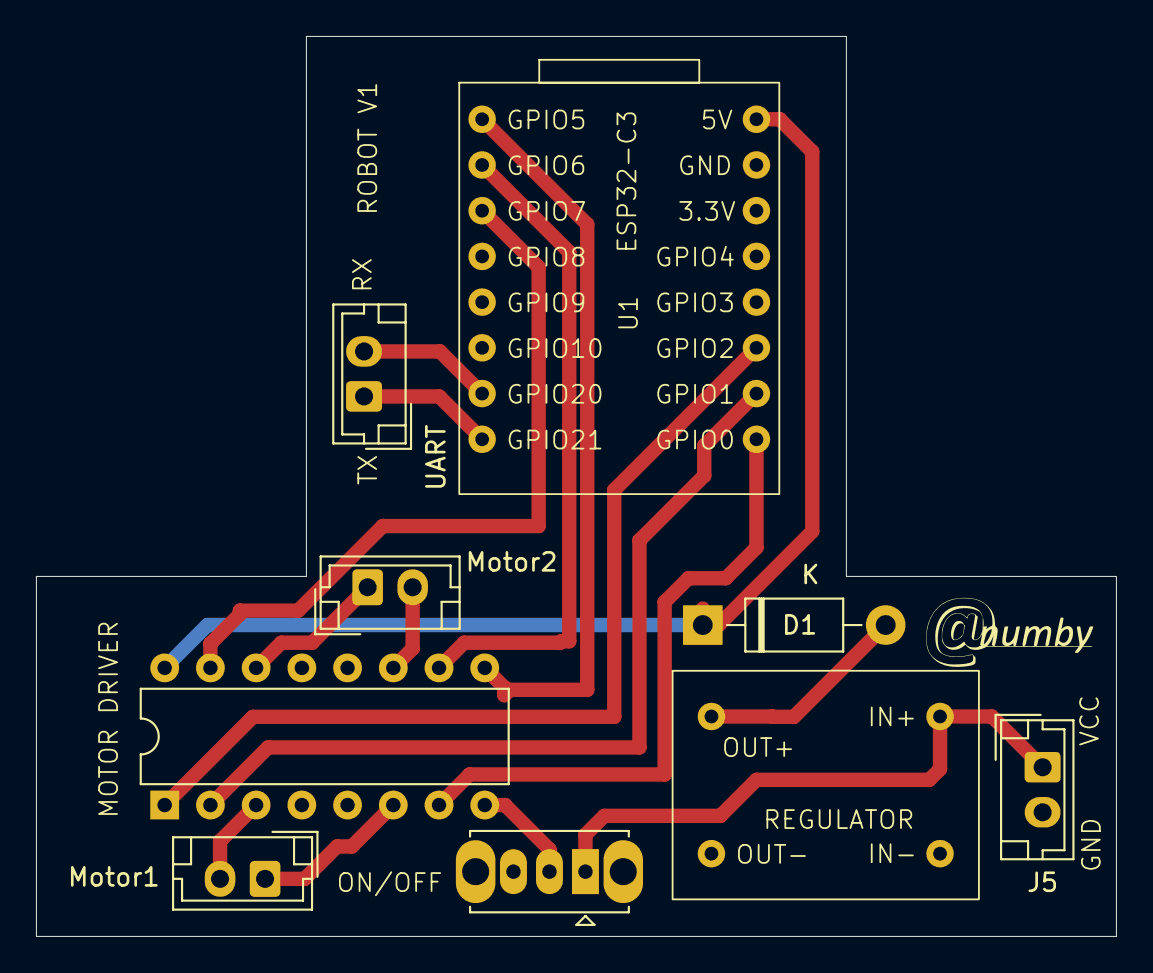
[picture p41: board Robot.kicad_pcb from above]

Board: 2 copper layers, 60.0 x 50.0 mm, 10 parts (0 on the bottom side), 17 nets.

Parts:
D1: 1N5818; D_DO-41_SOD81_P10.16mm_Horizontal
G: Val**; Logo_Anumby_10
J5: Conn_01x02_Socket_H; JST_EH_B2B-EH-A_1x02_P2.50mm_Vertical
Motor1, Motor2: Conn_01x02_Socket_H; JST_EH_B2B-EH-A_1x02_P2.50mm_Vertical
SW1: SW_DPDT_x2; SW_Slide_SPDT_Straight_CK_OS102011MS2Q
U1: ESP32-C3_SUPERMINI
U2: L293D; DIP-16_W7.62mm
U4: REG_5V; REG_5V_DFR
UART: Conn_01x02_Socket_H; JST_EH_B2B-EH-A_1x02_P2.50mm_Vertical

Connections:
GND: J5.2, U1.2 (GND), U2.4 (GND), U2.5 (GND), U4.2 (GND), U4.4 (GND)
unnamed: D1.2 (A), U4.3 (+VOUT)
unnamed: D1.1 (K), U1.1 (5V), U2.16 (VCC1)
unnamed: U1.9 (GPIO21), UART.1
unnamed: U1.10 (GPIO20), UART.2
unnamed: Motor2.1, U2.14 (4Y)
unnamed: Motor2.2, U2.11 (3Y)
unnamed: Motor1.1, U2.6 (2Y)
unnamed: Motor1.2, U2.3 (1Y)
unnamed: J5.1, SW1.1 (A), U4.1 (+VIN)
unnamed: SW1.2 (B), U2.8 (VCC2)
unnamed: U1.8 (GPIO0), U2.7 (2A)
unnamed: U1.7 (GPIO1), U2.2 (1A)
unnamed: U1.6 (GPIO2), U2.1 (EN1,2)
unnamed: U1.16 (GPIO5), U2.9 (EN3,4)
unnamed: U1.15 (GPIO6), U2.10 (3A)
unnamed: U1.14 (GPIO7), U2.15 (4A)

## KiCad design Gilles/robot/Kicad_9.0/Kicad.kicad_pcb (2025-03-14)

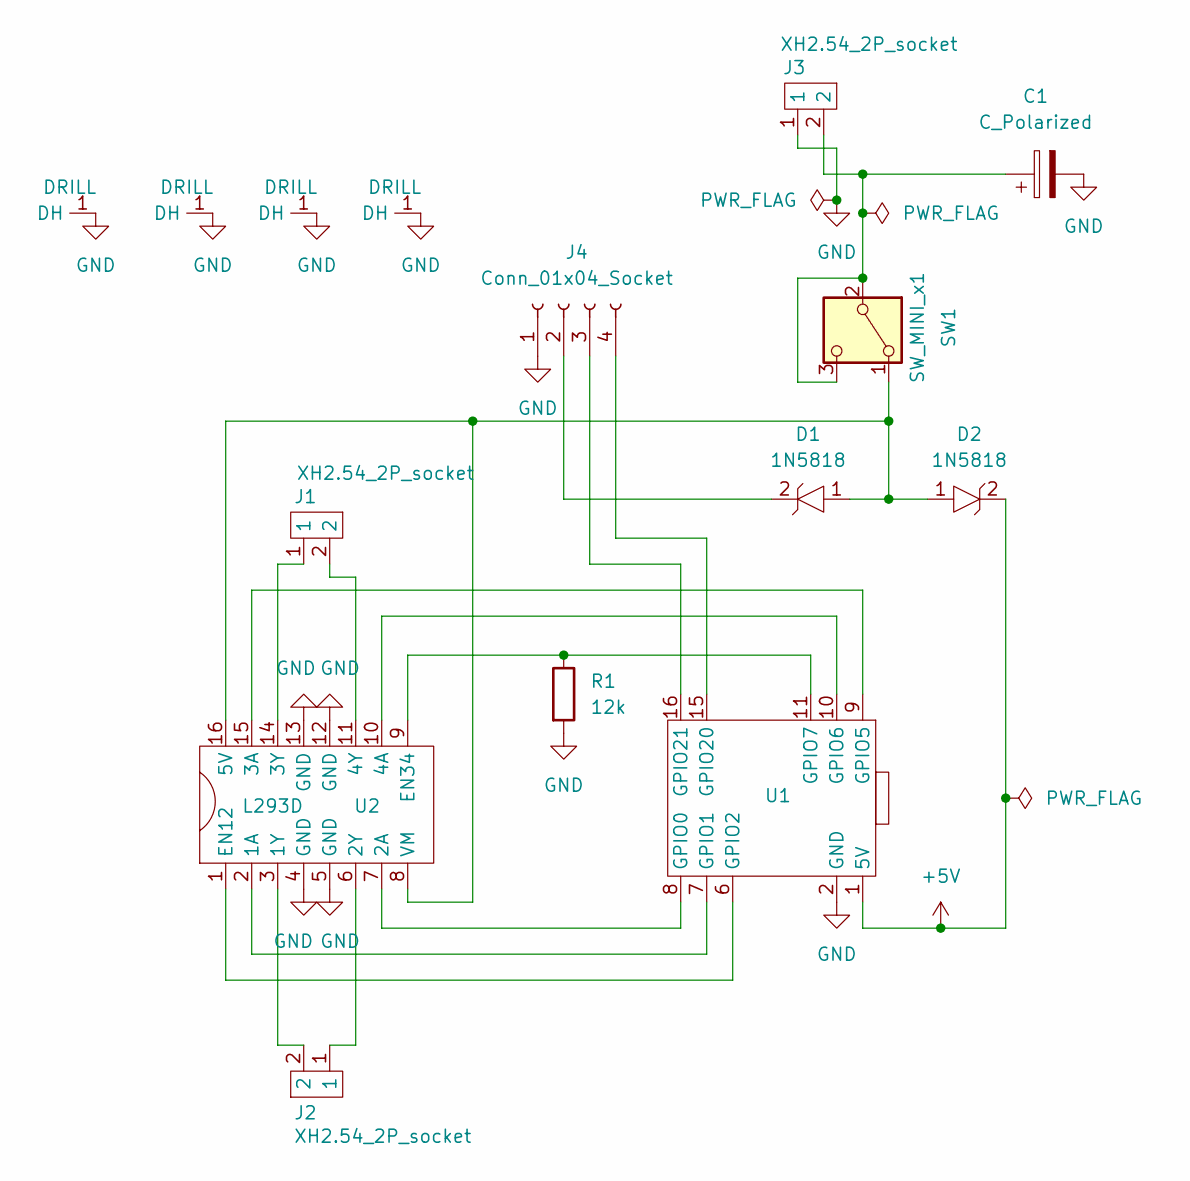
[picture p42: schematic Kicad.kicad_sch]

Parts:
C1: C_Polarized; CP_8mm_3.5mm
D1, D2: 1N5818
DH1, DH2, DH3, DH4: DRILL; DRILL_HOLE
J1, J2, J3: XH2.54_2P_socket; XH2.54_2P_soc
J4: Conn_01x04_Socket; NS-Tech_Grove_1x04_P2mm_Vertical
R1: 12k; 1N5818
SW1: SW_MINI_x1; SW_MINI_X1
U1: ESP32-C3_SUPERMINI
U2: L293D

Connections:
+5V: D2.2, U1.1 (5V)
GND: C1.2, DH1.1 (DH), DH2.1 (DH), DH3.1 (DH), DH4.1 (DH), J3.1, J4.1, R1.2, U1.2 (GND), U2.4 (GND), U2.5 (GND), U2.12 (GND), U2.13 (GND)
unnamed: D1.2, J4.2
unnamed: J4.3, U1.16 (GPIO21)
unnamed: J4.4, U1.15 (GPIO20)
unnamed: D1.1, D2.1, SW1.1 (A), U2.8 (VM), U2.16 (5V)
unnamed: C1.1, J3.2, SW1.2 (B), SW1.3 (C)
unnamed: U1.8 (GPIO0), U2.7 (2A)
unnamed: U1.7 (GPIO1), U2.2 (1A)
unnamed: U1.6 (GPIO2), U2.1 (EN12)
unnamed: U1.9 (GPIO5), U2.15 (3A)
unnamed: U1.10 (GPIO6), U2.10 (4A)
unnamed: R1.1, U1.11 (GPIO7), U2.9 (EN34)
unnamed: J2.2, U2.3 (1Y)
unnamed: J2.1, U2.6 (2Y)
unnamed: J1.1, U2.14 (3Y)
unnamed: J1.2, U2.11 (4Y)

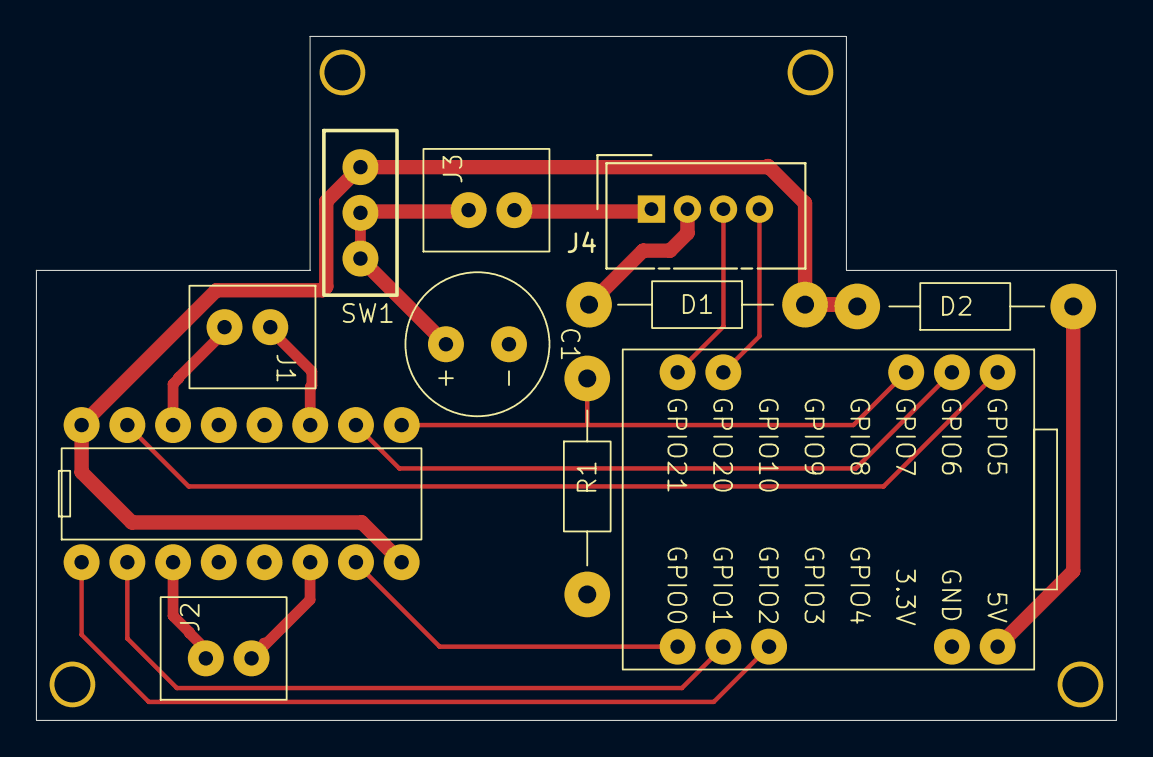
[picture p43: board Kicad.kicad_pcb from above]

Board: 2 copper layers, 60.0 x 38.0 mm, 15 parts (0 on the bottom side), 17 nets.

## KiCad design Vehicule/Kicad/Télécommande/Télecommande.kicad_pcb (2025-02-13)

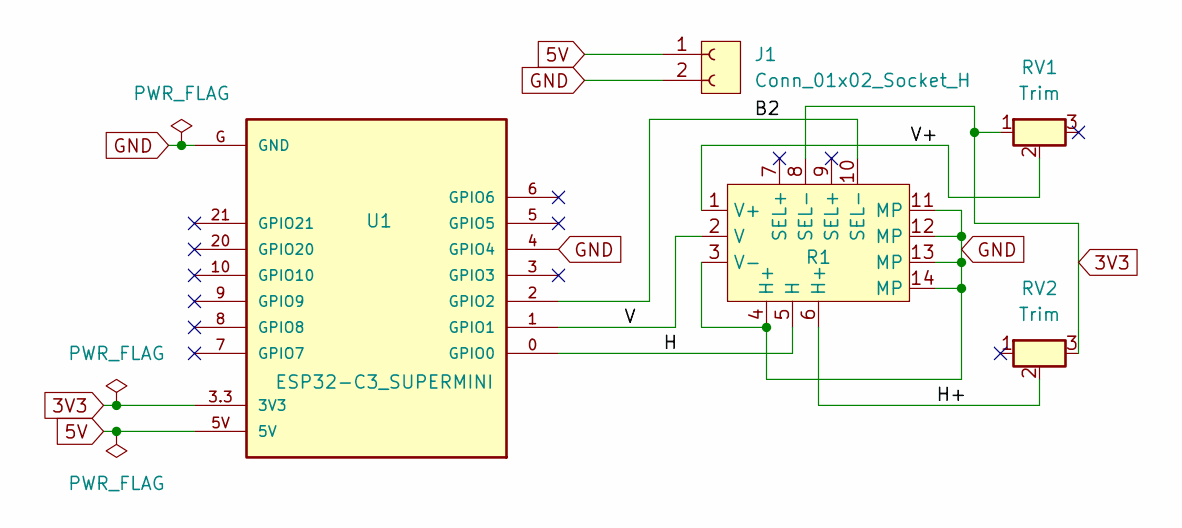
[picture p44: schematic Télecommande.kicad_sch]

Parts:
J1: Conn_01x02_Socket_H; JST_PH_S2B-PH-K_1x02_P2.00mm_Horizontal
R1: JOYSTICK_MODEL_802
RV1, RV2: Trim; Potentiometer_Runtron_RM-065_Vertical
U1: ESP32-C3_SUPERMINI; ESP32-C3-SUPERMINI

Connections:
3V3: R1.8 (SEL-), RV1.1, RV2.3, U1.3.3 (3V3)
5V: J1.1, U1.5V
/B2: R1.10 (SEL-), U1.2 (GPIO2)
/H: R1.5 (H), U1.0 (GPIO0)
/H+: R1.6 (H+), RV2.2
/V: R1.2 (V), U1.1 (GPIO1)
/V+: R1.1 (V+), RV1.2
GND: J1.2, R1.3 (V-), R1.4 (H+), R1.11 (MP), R1.12 (MP), R1.13 (MP), R1.14 (MP), U1.4 (GPIO4), U1.G (GND)

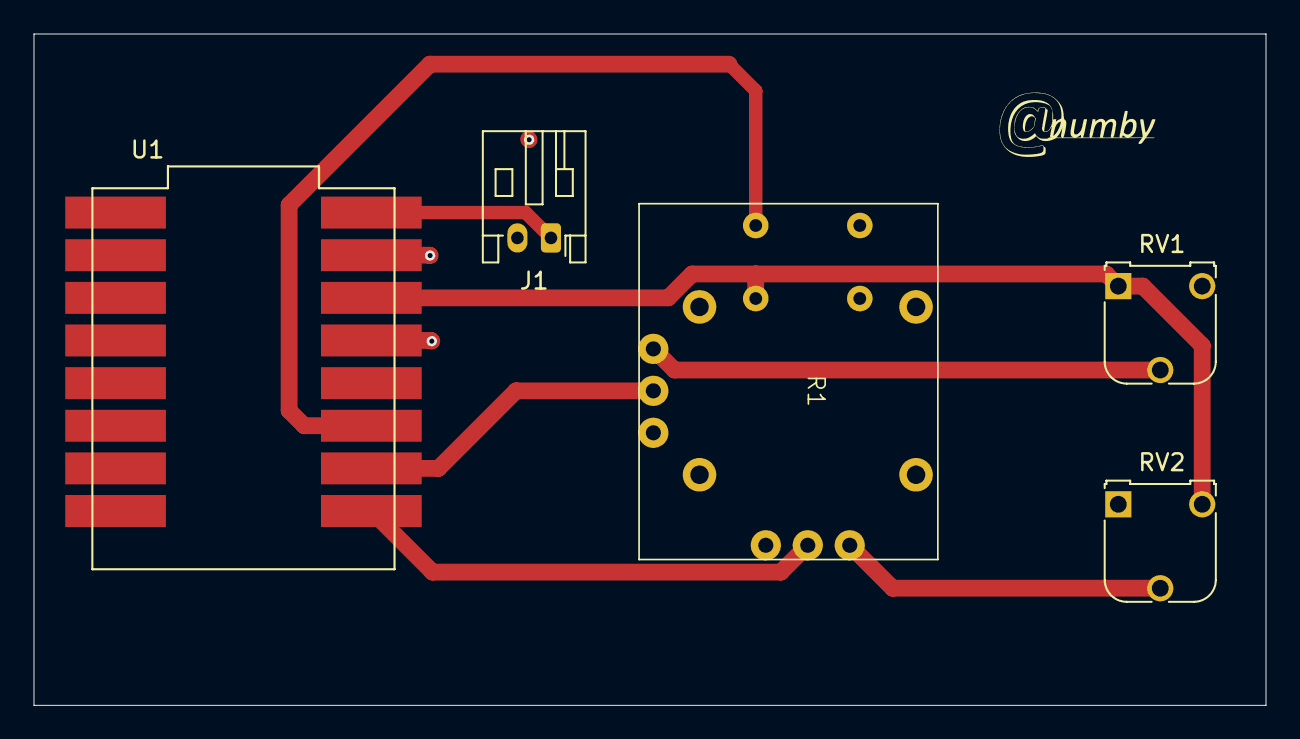
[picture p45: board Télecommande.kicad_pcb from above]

Board: 2 copper layers, 73.4 x 40.0 mm, 6 parts (0 on the bottom side), 8 nets.

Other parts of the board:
G: Val**; Logo_Anumby_10

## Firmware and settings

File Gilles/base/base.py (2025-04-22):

import sys
import network
import espnow
from time import sleep_ms
from machine import Pin
from mac_addr import robot_mac

# mac = b'$X|\x91\xe0\xd8'  # base MAC address
mac_robot = {}
for e in robot_mac.items():
    mac_robot[e[1]] = e[0]
# espnow init
sta = network.WLAN(network.STA_IF)
sta.active(True)
e = espnow.ESPNow()
e.active(True)
print('espnow ok')
# led init
led = Pin(8, Pin.OUT)
led.on()    # led off
#
while True:
  addr, msg = e.recv()
  if addr:
#      print('msg:', msg)
      l = msg.split(b'\n')
      if len(l) == 2:
          ville = l[0]
#          print('ville:', ville)
          print("{}:{}".format(mac_robot[addr], ville.decode()))

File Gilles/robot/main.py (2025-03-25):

# Put your code here

#################################
# def start_robot(e):
#     Pin(9, Pin.IN).irq(handler=None, trigger=Pin.IRQ_FALLING)
#     import robot
#
# from machine import Pin
# irq = Pin(9, Pin.IN).irq(handler=start_robot, trigger=Pin.IRQ_FALLING)
#################################
# mac = b'$X|\x91\xe3`'   # this device

import robot

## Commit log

2024-05-28 Mise en place de la structure de développement . En commençant par la structure de R&D
2025-01-29 Ajoute la liste des composants à acheter pour la fabrication du véhicule
2025-01-29 Première version de circuits électroniques pour la télécommande et pour le véhicule (à associer avec la liste BOM)
2025-01-29 Addition des composants pour le ESP32-C3-SUPERMINI. Utilisation de ce module dans le projet Kicad
    [Télécommande.kicad_pcb, Télécommande.kicad_sch]
2025-01-30 Création du joystick Ajout du joystick Ajout des trimmers
    [Télécommande.kicad_sch]
2025-01-30 Update de .gitignore
2025-02-02 Empeinte du joystick
    [Télécommande.kicad_sch]
2025-02-02 Pour le joystick ou récupère les documents au format EAGLE mais on n'arrive pas à les convertir au format KiCad. Donc on transfert manuellement les données de l'empreinte.
    [Joystick-Breakout-v12.brd, Joystick-Breakout-v12.sch]
2025-02-02 BOM: mise au format MD
2025-02-02 Compléter le schéma
    [Télécommande.kicad_sch]
2025-02-05 Suppression des anciennes versions du projet Télécommande
    [Télécommande.kicad_pcb, Télécommande.kicad_sch]
2025-02-06 Un peu de ménage dans les dossiers
    [Joystick-Breakout-v12.brd, Joystick-Breakout-v12.sch]
2025-02-06 Schema et implantation du circuit pour le robot ajoute un dossier pour le projet Kicad pour la télécommande
    [Télecommande.kicad_pcb, Télecommande.kicad_sch]
2025-02-06 Schema et implantation du circuit pour le robot
    [Robot.kicad_pcb, Robot.kicad_sch]
2025-02-06 La librairie Kicad Anumby avec les composants ajoutés Cette librairie est associée à la librairie d'empreintes
2025-02-07 Transfert du SUPERMINI (composant et empreintes) dans les librairies locales (Anumby et Empreintes)
2025-02-07 Transfert du SUPERMINI (composant et empreintes) dans les librairies locales (Anumby et Empreintes) Renommer Empreintes -> Anumby
2025-02-10 TAjouter la couche de masse pour la télécommande
    [Télecommande.kicad_pcb, Télecommande.kicad_sch]
2025-02-10 Ajout de la couche de masse pour Robot Ajout d'un connecteur 1 pin Mise à jour de tous les PCB et les Schémas
    [Robot.kicad_pcb, Robot.kicad_sch, Télecommande.kicad_pcb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]
2025-02-11 Ajout de logo Anumby pour PCB (2 versions)
    [Robot.kicad_pcb, Télecommande.kicad_pcb, pogo_pin.step]
2025-02-12 Ajout de logo Anumby pour PCB
    [Robot.kicad_pcb]
2025-02-13 Ajout de logo Anumby pour PCB Mise à jour des empreintes, des connecteurs des librairies
    [Robot.kicad_pcb, Robot.kicad_sch, Télecommande.kicad_pcb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]
2025-02-13 Finalisation du PCB de la Télécommande puis génération des fichiers de fabrication Gerber
    [Télecommande-B_Cu.gbl, Télecommande-B_Mask.gbs, Télecommande-B_Paste.gbp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]
2025-02-13 Finalisation du PCB du Robot puis génération des fichiers de fabrication Gerber
    [Robot-B_Cu.gbl, Robot-B_Mask.gbs, Robot-B_Paste.gbp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]
2025-02-18 Ajout d'un titre ROBOT / TELECOMMANDE et d'une version (V1) sur la sérigraphie
    [Robot-B_Cu.gbl, Robot-B_Mask.gbs, Robot-B_Paste.gbp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]
2025-02-18 Remplacement de l'empreinte ESP32 de surface pour une empreinte traversante
    [Robot-B_Cu.gbl, Robot-B_Mask.gbs, Robot-B_Paste.gbp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]
2025-03-18 Modification des fichiers Kicad de Gilles Premier test de la gestion de l'historique du trajet Chris/robot.py
    [Robot-B_Cu.gbl, Robot-B_Mask.gbs, Robot-B_Paste.gbp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]
2025-03-18 Simulation du programme robot.py - avec motor - avec détection de ville - 6 villes, trajet jusqu'à la détection de la dernière ville
2025-03-18 Simulation du programme robot.py - avec motor - avec détection de ville - 6 villes, trajet jusqu'à la détection de la dernière ville - impression de l'historique ordonné
2025-03-19 Simulation du programme robot.py - paramètre VILLES = nombre max de villes - implémentation de 2 algorithmes: 1) détection des villes à partir de la ville 1 jusqu'à la ville VILLES mais sans ordre in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
2025-03-19 Rename fixation moteur N20 v3.stl to fixation moteur.stl
    [fixation moteur.stl]
